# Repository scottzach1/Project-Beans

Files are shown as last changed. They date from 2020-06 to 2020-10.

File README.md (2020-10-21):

# Group 3 - Project beans

## Welcome to Project Beans.

Project Beans was a 2020 project by 6 VUW Engineering students to
deliver a model rocket for a client. An in-depth breakdown of the
projects scope, deliverables and current state can be obtained in-depth
within the documentation of this repository.

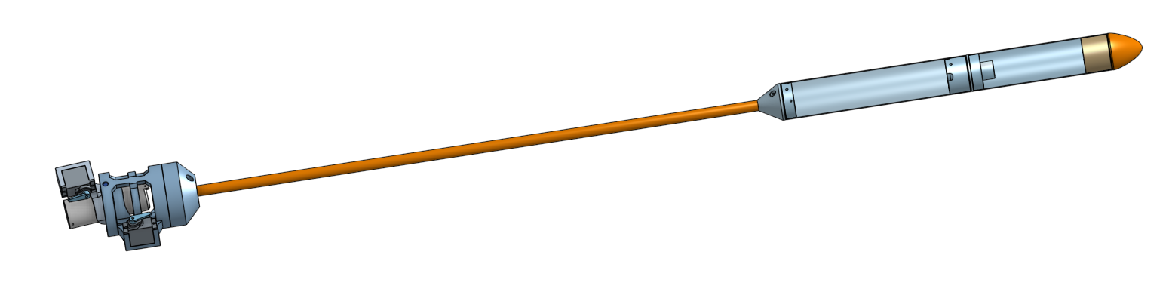
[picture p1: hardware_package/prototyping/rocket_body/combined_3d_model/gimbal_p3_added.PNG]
Rocket Design


> Figure 1: Rocket Design Render

## Meet The Team

### Software

| Zac Scott (https://github.com/scottzach1) | Ron Crisostomo (https://github.com/crisosron) | Finlay Sargisson (https://github.com/sarrgi) |
|:---|:---|:---|
| [Zac Scott](https://github.com/scottzach1) | [Ron Crisostomo](https://github.com/crisosron) | [Finlay Sargisson](https://github.com/sarrgi) |

### Hardware

| Niels Clayton (https://github.com/Niels-Clayton) | William Fowler (https://github.com/Will-Fowler) | Billy Rob (https://gitlab.ecs.vuw.ac.nz/robbbill) |
|:---|:---|:---|
| [Niels Clayton](https://github.com/Niels-Clayton) | [William Fowler](https://github.com/Will-Fowler) | [Billy Rob](https://gitlab.ecs.vuw.ac.nz/robbbill) |

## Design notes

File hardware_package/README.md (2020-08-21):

# Hardware Package

This directory is for all hardware related files, such as PCB designs,
CAD files etc...

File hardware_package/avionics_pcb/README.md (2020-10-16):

# Avionics PCB's

> Description of the different avionics PCB's and libraries

## KiCad

- All PCB's will be designed using the KiCad Cross Platform and Open Source Electronics Design Automation Suite. A selection of custom footprints and symbols used in the following projects can be found in the `kicad_lib/` directory.

- All PCB's within this directory will be subject to standard ERC and DRC rule checks, which will be performed and checked by the CI pipeline.

## PCB's

| File | Description |
|:---|:---|
| `avionics_base_station/`  | The avionics base station PCB will be used to connect the RFM98 LoRa radio to the [ESP8266 microcontroller](https://www.espressif.com/en/products/socs/esp8266), maintaining a small form-factor. This board is designed to be the final base station product. |
| `avionics_breakout_PCB/`  | The avionics breakout PCB will is the second prototype of the rocket hardware. This PCB will take all of the testing breakout boards that can be found [here](../bill_of_materials/bill_of_materials.md) in the BOM, and will integrate all of then onto a single compact board that is limited to a single side. This board will be used for extensive testing of the hardware in unison. |
| `Final_PCB/` | The avionics final PCB is the final iteration of the PCB. This board will take all of the individual components found on each of the breakouts, and will place them onto a single PCB. This board will also include power supplies for all components, including the ignition circuitry and servo motors.  |

## Libraries

| File | Description |
|:---|:---|
| `kicad_lib/` | This directory contains a selection of custom footprints and symbols that have been used in the PCB's. This library currently contains footprints for the following parts:

- Adafruit Feather STM32F4D5 Breakout
- ESP8266 Node MCU microcontroller breakout
- Adafruit MPL3115A2 Barometer Breakout
- Adafruit MPU 6050 Breakout
- RFM98 LoRa Radio

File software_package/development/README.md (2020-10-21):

## Development

The project structure  is covered in the `software_package` 
[README](../README.md), if you wish to understand more about this then 
go there. This README entails an overview of each of our libraries which 
can be found inside this package.

### Hardware

This library is specific to the exact hardware components which we have
used for this project. The key goal of this is to provide an API which
allows for abstraction away from the specifics parts for each type of
hardware component. For example, through this library the software
library is able to interact with the MPU-6050 by treating it as any IMU.
You're able to find the exact hardware library which is being abstracted
away from inside of `.pio/libdeps`.

Each component is represented with a header file (.h), as well as a
concrete implementation (.cpp). This separation of components allows for
maximum flexibility and reuse. If one specific component is upgraded or
replaced then only the relative header and implementation file should
need modifying.

### Current State

Towards the end of development for this project, there was a significant
update to platformio that changed how some of the libraries were
handled. This change, inherently broke the builds on a lot of the team
members devices. For some devices, this can be mitigated by installing
the `Servo` package to the project locally. Then manually moving it into
the `~/.platformio/lib/` directory (global libraries). There were
occasionally issues regarding the i2cdev libraries for the MPU6050 after
integration with the rest of the code base.

### Component Library Breakdown

| Component | Description |
|:---:|:---|
| Barometer | This is based off of the `Adafruit_MPL3115A2.h` library. The key functionality of this is reading air pressure and altitude data. |
| IMU | This was originally based off of the `Adafruit_MPU6050.h` library. To get more accurate readings this has since been switched to `I2Cdevlib-Core` and `I2Cdevlib-Core`. This allows us to be able to read quaternion values that are inherently less prone to errors and gimbal lock. In general, the main purpose of this is to perform the accelerometer and gyroscope readings. |
| Parachute | This component is still in development, but aims to simply handle the launching of the parachute ejection charges. |
| SD | This is based off of the `STM32SD.h` library. The primary functionality for this is performing file reading and writing on the SD card. |
| Servo | This makes use of the `Servo.h` library. The goal of this component here is adjusting and controlling the angle of the servo. |

### Software

This library aims to handle all the logic for our rocket, and works in
tandem with the hardware library to achieve this. As it is more
abstracted away than the hardware library it is designed to be robust
enough to be used with different hardware components. Small things, eg.
tuning a value to match a new part speed, may need updating when
replacing and upgrading components, but the core logic should be
relatively versatile.

| Component | Description |
|:---:|:---|
| Debug | This file is used for debugging messages related to our hardware. It can be used for writing and testing code, as well as pre-, post- and in-flight analysis. |
| States and State Machine | The state machine handles the current state of the rocket, and how to transition between them. States contains all potential states the rockets' system can be in. For a more in-depth explanation see section 4.1 of the [architecture](../../architecture_design/architecture-design.md) document, which covers the flow this software is modelled around. |
| Guidance System | This is essentially the main process of our rocket. It handles all the logic necessary to function, such as the pid, state machine, and all hardware communication. |
| Logging | This component handles sending data to both the SD card and LoRa radio. |

### Installed Packages
```bash
'Adafruit GFX Library'/
'Adafruit ILI9341'/
'Adafruit BusIO'/
'Adafruit MPL3115A2 Library'/
'Adafruit STMPE610'/
'Adafruit TouchScreen'/
'FatFs'/
'I2Cdevlib-Core'/
'I2Cdevlib-MPU6050'/
'STM32duino STM32SD'/
```

How to build PlatformIO based project
=====================================
Keep in mind that this entire directory _is_ a PlatformIO project. The steps below
outline how to build this project.

1. `Install PlatformIO Core <http://docs.platformio.org/page/core.html>`_
2. Download `development platform with examples <https://github.com/platformio/platform-native/archive/develop.zip>`_
3. Extract ZIP archive
4. Run these commands:

```bash
    # Change directory to example
    > cd platform-native/examples/hello-world

    # Build project
    > platformio run

    # Run program
    > .pioenvs/native/program

    # Clean build files
    > platformio run --target clean
```

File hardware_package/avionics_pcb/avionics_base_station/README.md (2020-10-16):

# Avionics Base Station PCB

This PCB is designed to interface the NodeMCU microcontroller with the RFM98 radio module. This board will act as the base station that will connect the ground control computer.

This PCB has been designed for a single layer, meaning that it is feasible to mill this PCB.

To assemble this unit, either directly solder the NodeMCU unit to the board, or solder on female headers with which to connect it. Then solder on the RFM98 castellated module and connect a solid core wire to the antenna.

## Schematic

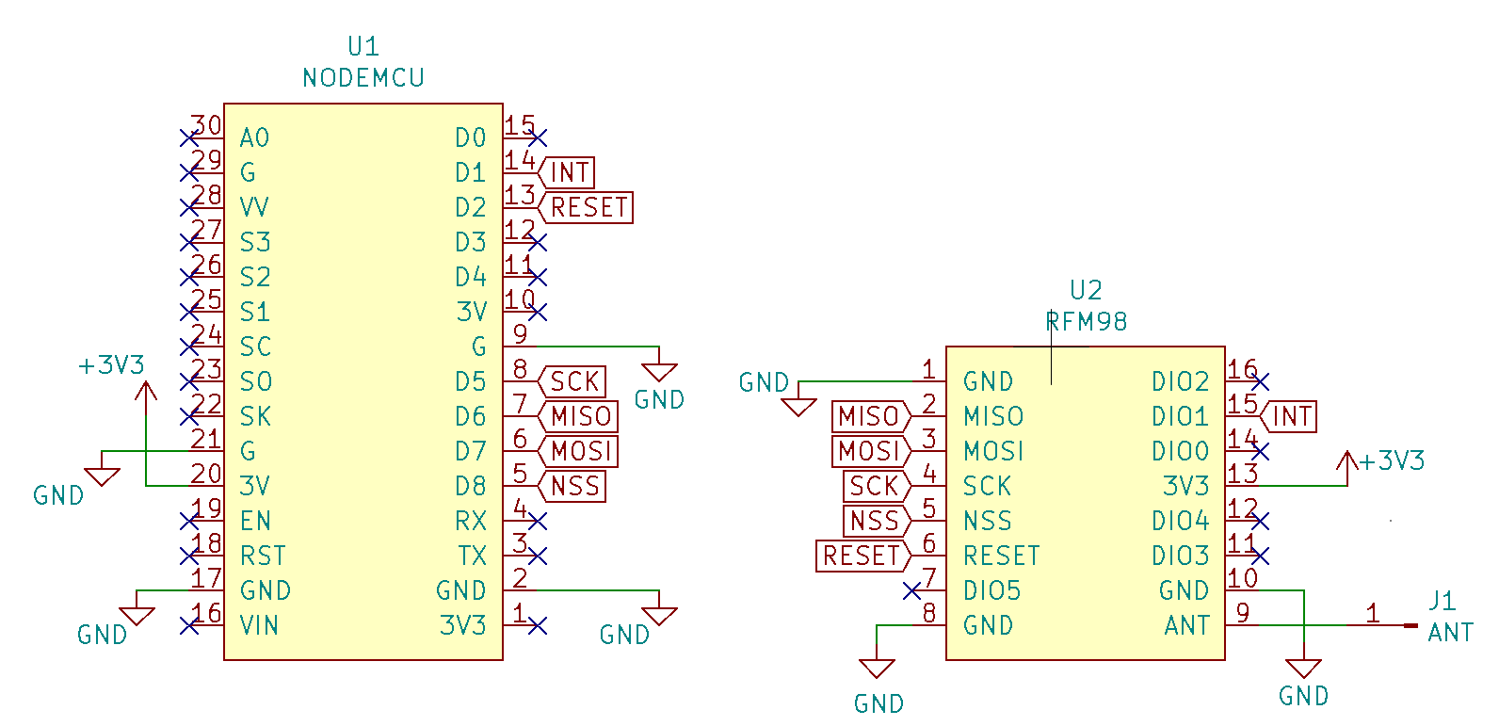
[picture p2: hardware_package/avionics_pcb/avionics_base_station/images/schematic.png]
schematic


## PCB Routing

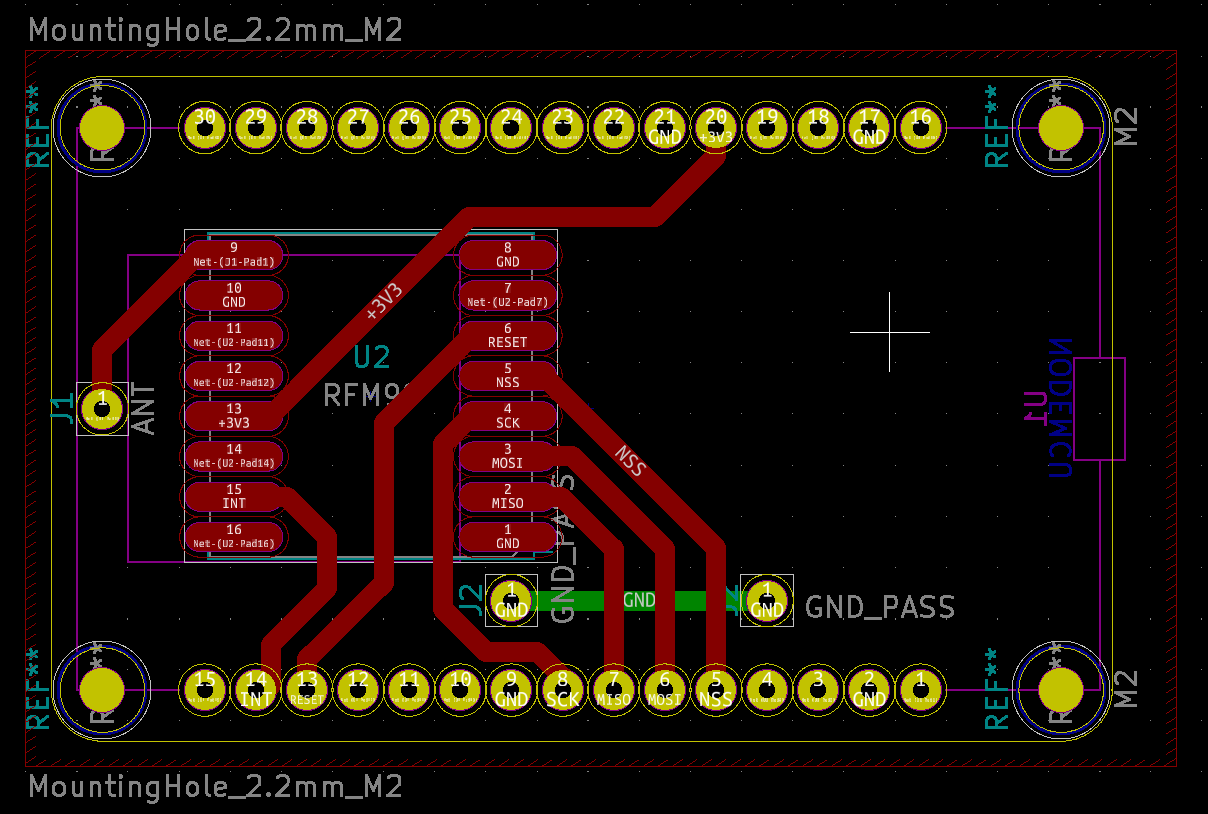
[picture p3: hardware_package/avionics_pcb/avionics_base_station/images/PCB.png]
PCB
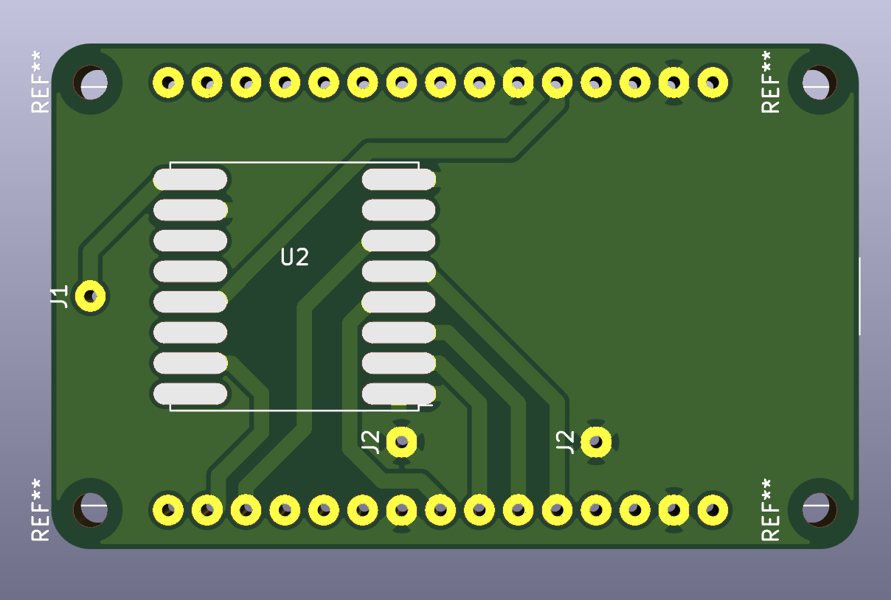
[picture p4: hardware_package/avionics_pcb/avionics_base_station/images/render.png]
render
 

## Assembled Unit

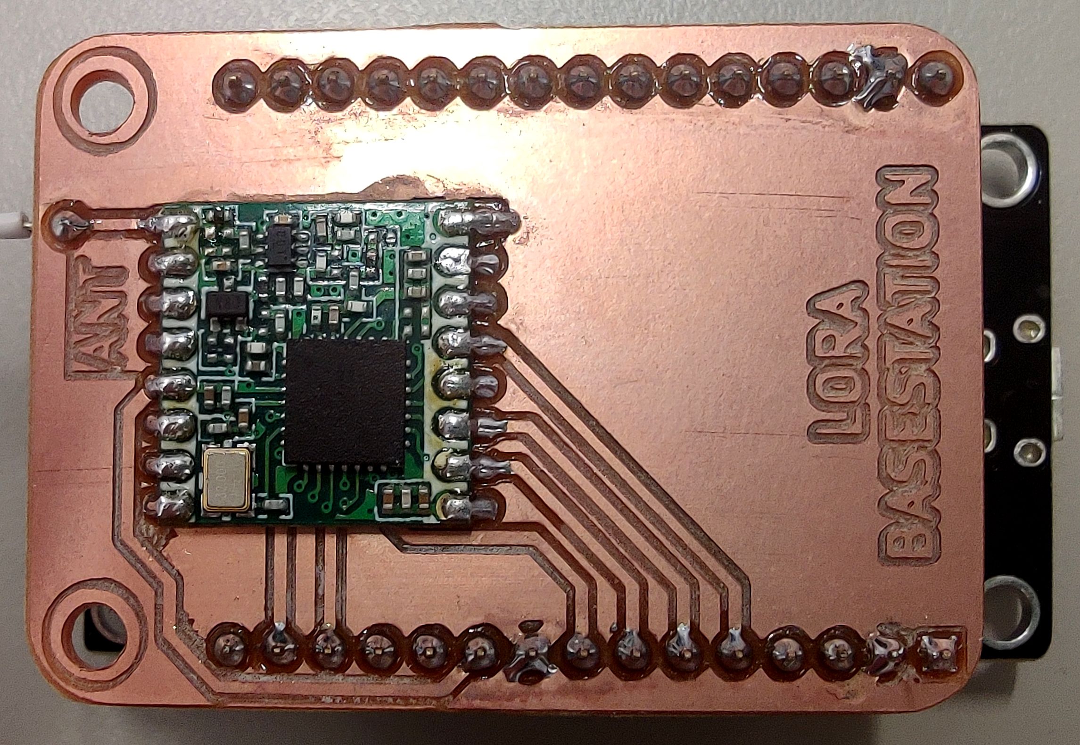
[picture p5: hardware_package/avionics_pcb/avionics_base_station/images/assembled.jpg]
assembled


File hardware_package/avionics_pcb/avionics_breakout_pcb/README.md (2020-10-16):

# Avionics Component Breakout PCB

This PCB is the second iteration of the avionics PCB, and is designed to interface the FeatherSTM with the MPU605 IMU, MPL3115A2 Barometer, and RFM98 LoRa module. This PCB is also design to breakout the UART serial connection needed for the GPS, as well as connections to the gimbal servos and 4 ignition lines.

This PCB is designed to be milled, and is therefor almost completely single sided. There will however need to be one mod wire connected if this PCB is milled on one side, which will connect the LoRa interrupt line to the interrupt pin.

To assemble this unit, either directly solder the components to the board, or solder on female headers with which to connect them. Then solder on the RFM98 castellated module and connect a solid core wire to the antenna.

## Schematic

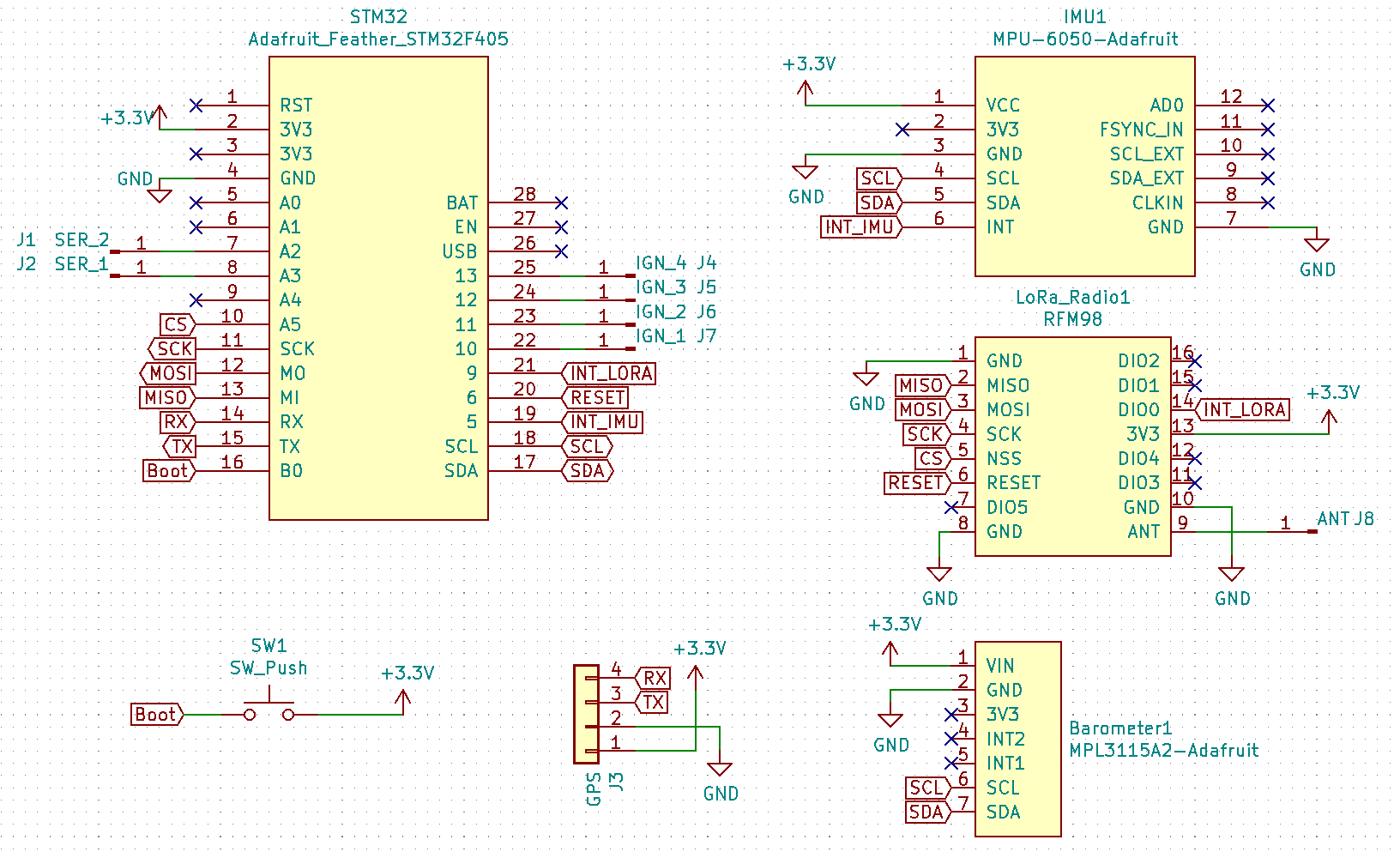
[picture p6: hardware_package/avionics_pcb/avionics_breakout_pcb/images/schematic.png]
schematic


## PCB Routing

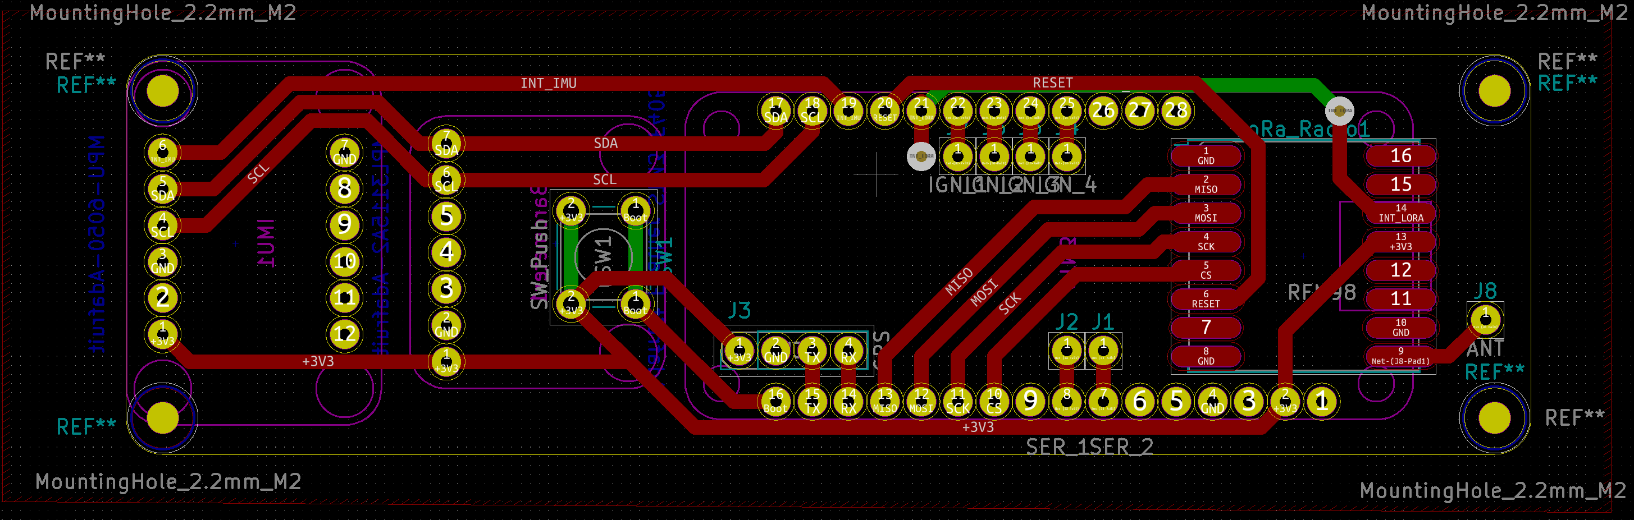
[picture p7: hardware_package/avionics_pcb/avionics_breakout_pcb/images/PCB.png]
PCB
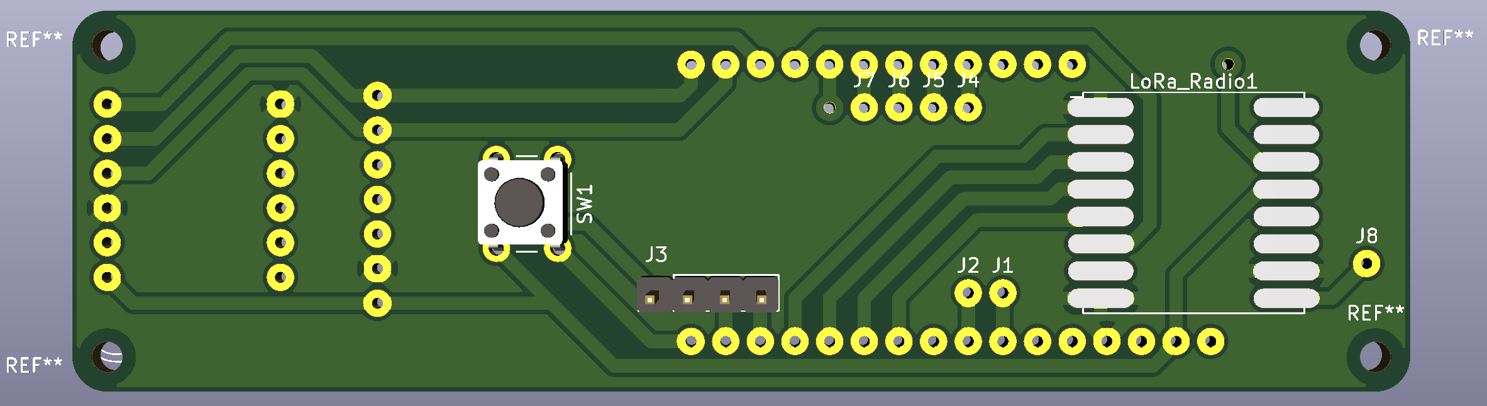
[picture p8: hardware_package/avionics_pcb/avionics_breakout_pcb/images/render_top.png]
render_top
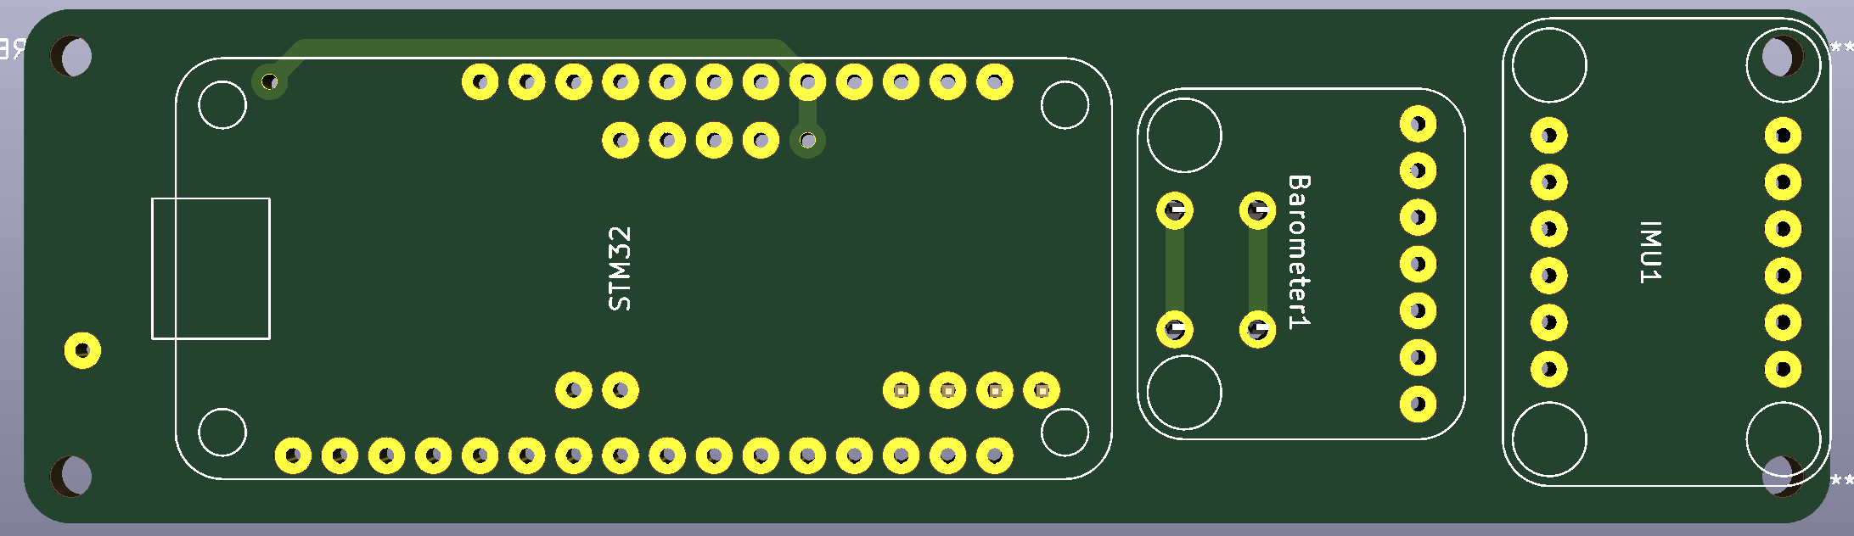
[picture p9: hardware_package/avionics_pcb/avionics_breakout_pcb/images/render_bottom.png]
render_bottom
  

## Assembled Unit

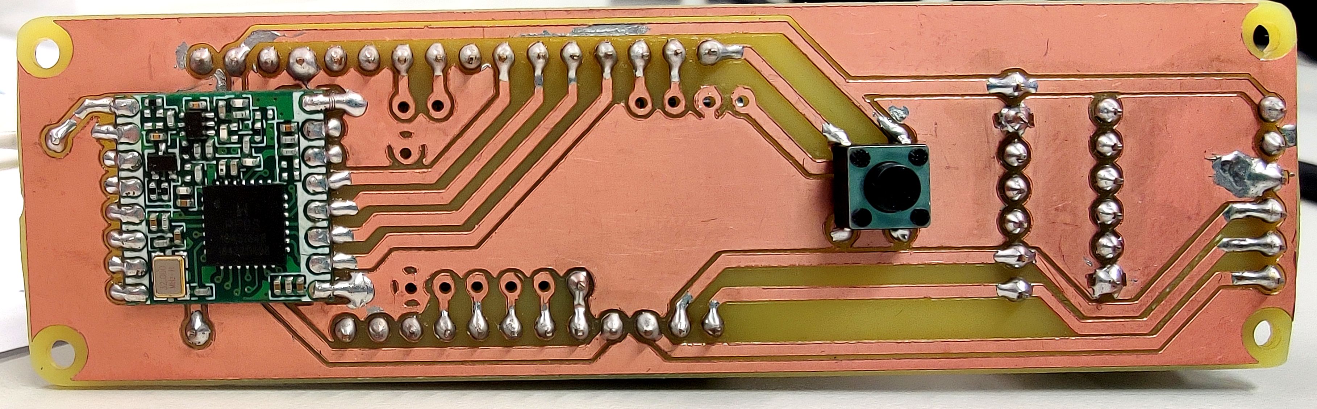
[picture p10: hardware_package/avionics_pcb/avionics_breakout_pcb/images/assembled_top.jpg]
assembled
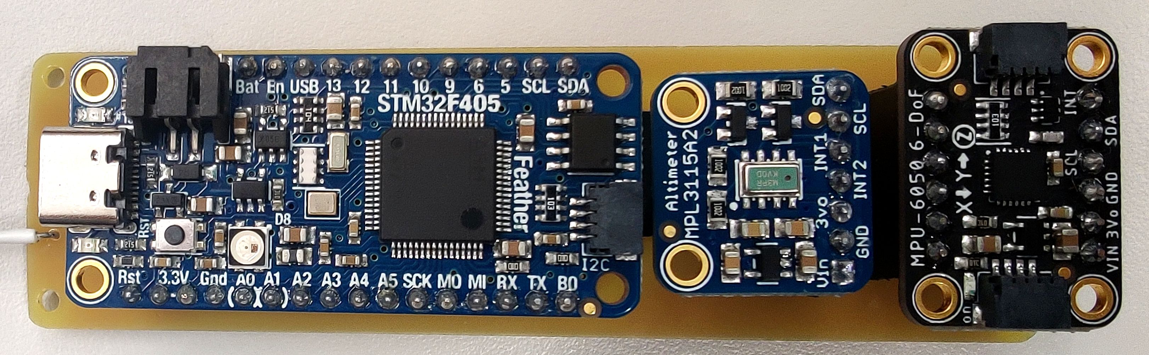
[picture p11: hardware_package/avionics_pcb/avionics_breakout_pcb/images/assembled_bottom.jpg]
assembled


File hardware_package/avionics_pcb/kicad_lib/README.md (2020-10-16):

# Avionics KiCad component library

This library contains all custom footprints and symbols that have been designed for use on the avionics PCB.

## Symbols

### Feather STM32 Breakout Symbol

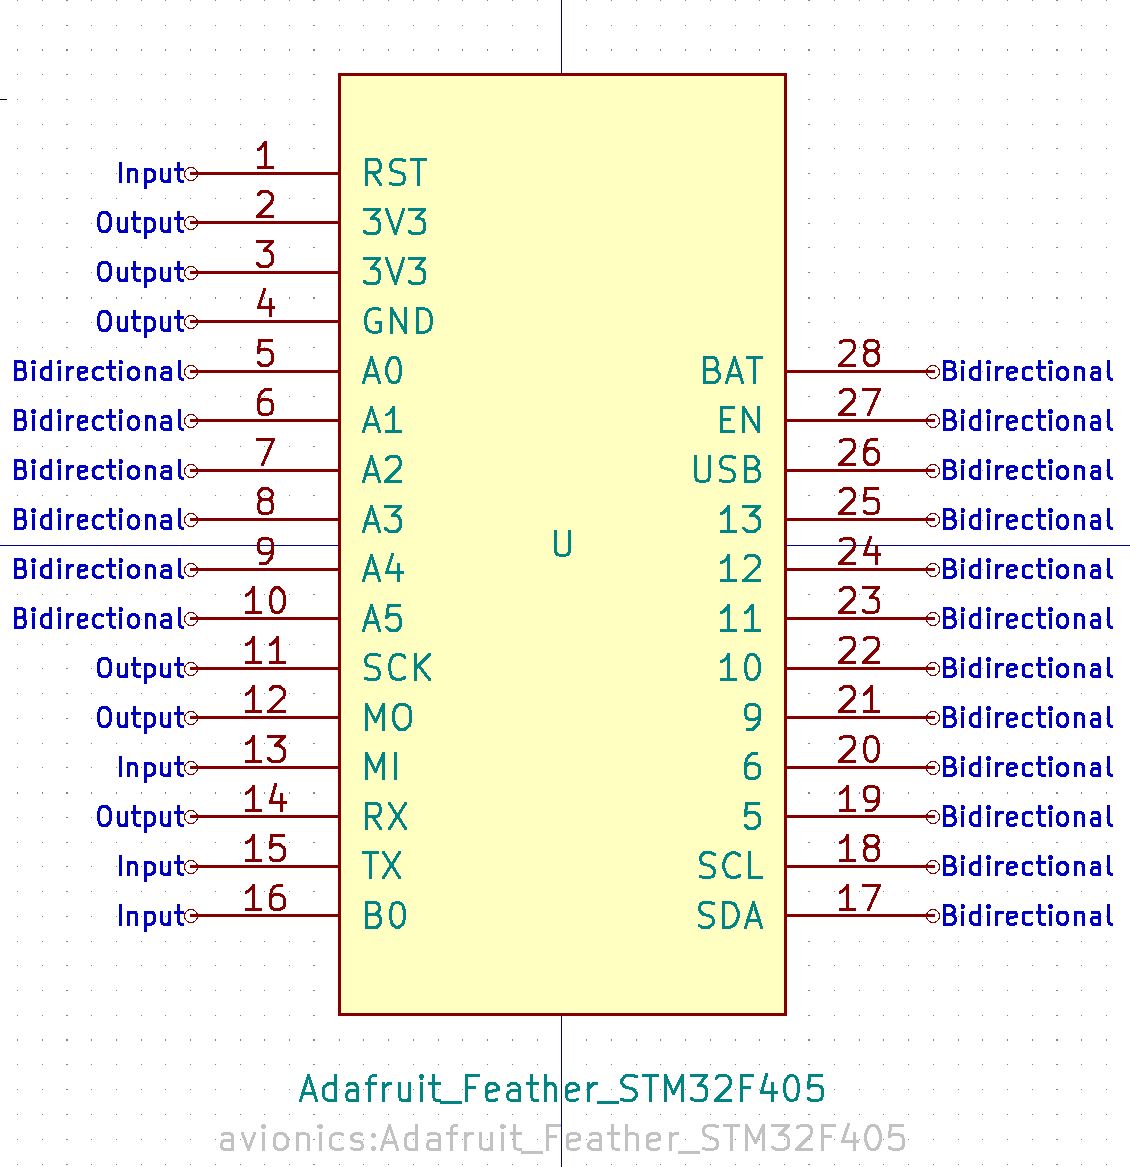
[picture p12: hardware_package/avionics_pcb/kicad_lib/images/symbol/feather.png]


### NodeMCU Breakout Symbol

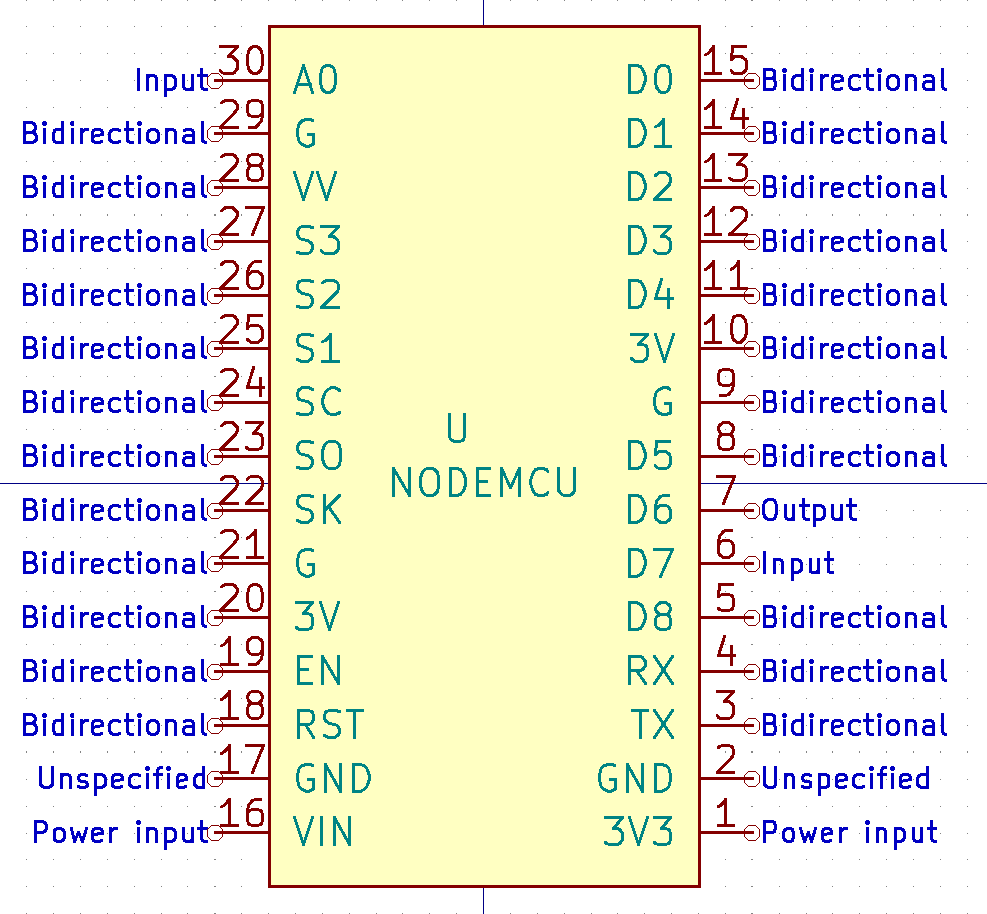
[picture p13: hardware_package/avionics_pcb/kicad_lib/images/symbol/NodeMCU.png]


### MPU6050 IMU Breakout Symbol

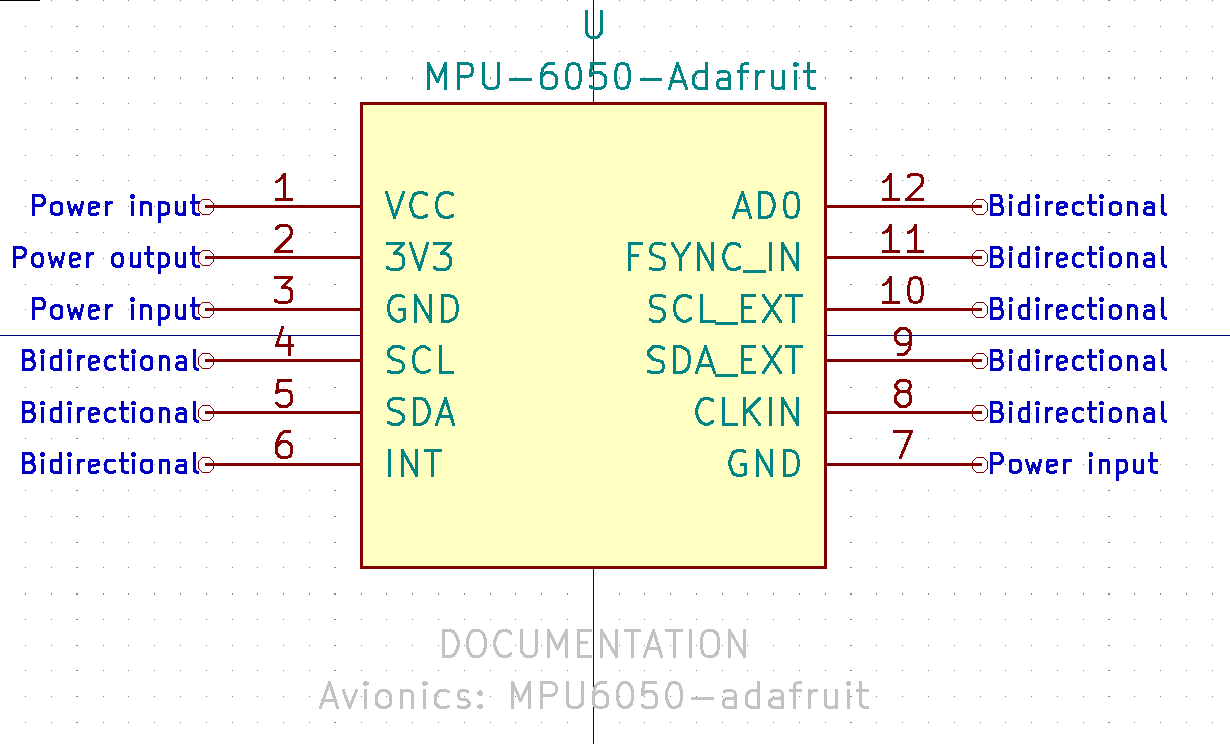
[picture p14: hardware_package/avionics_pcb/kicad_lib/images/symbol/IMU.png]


### MPL3115A2 Barometer Breakout Symbol

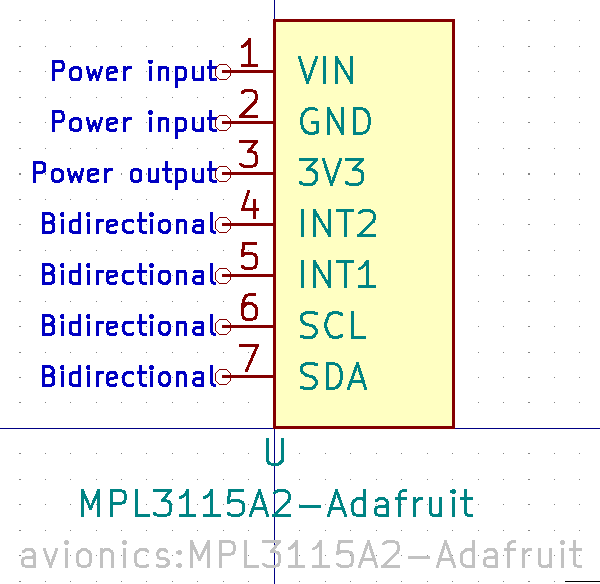
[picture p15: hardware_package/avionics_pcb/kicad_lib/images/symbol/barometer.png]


### RFM98 LoRa Radio Breakout Symbol

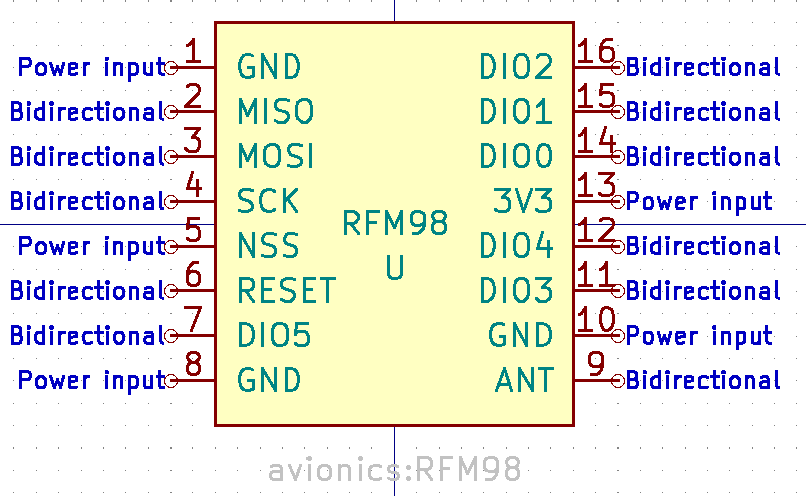
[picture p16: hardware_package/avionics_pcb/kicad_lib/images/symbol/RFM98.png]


## Footprints

### Feather STM32 Breakout Footprint

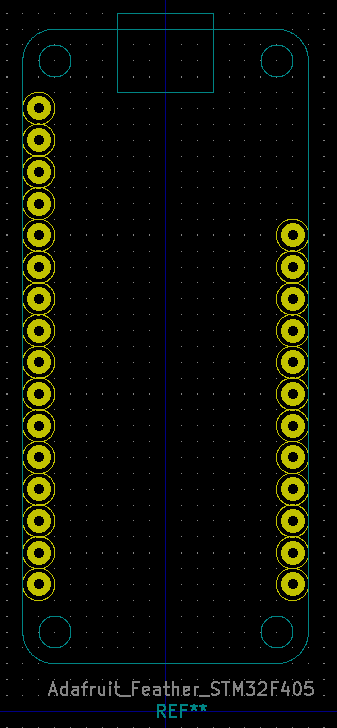
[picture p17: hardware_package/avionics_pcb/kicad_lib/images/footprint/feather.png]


### NodeMCU Breakout Footprint

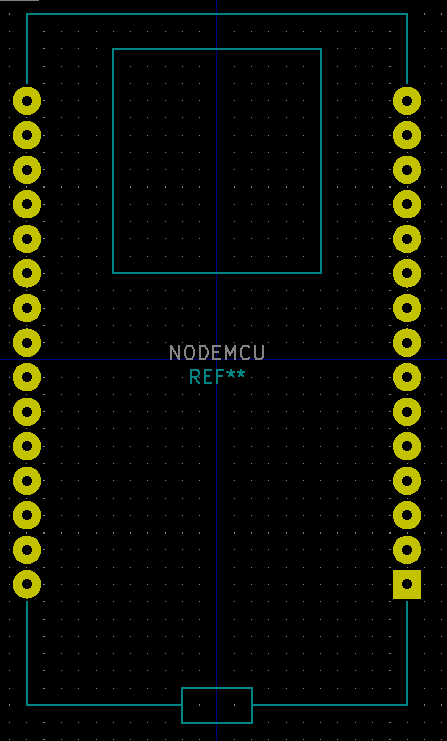
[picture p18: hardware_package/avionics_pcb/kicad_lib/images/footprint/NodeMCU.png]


### MPU6050 IMU Breakout Footprint

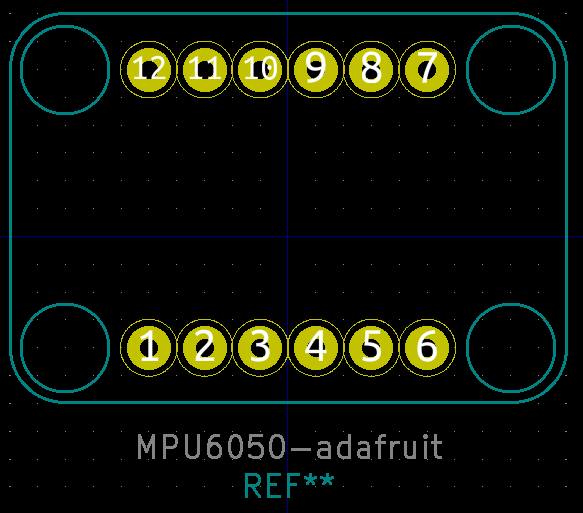
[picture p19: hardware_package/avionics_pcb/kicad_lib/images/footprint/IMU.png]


### MPL3115A2 Barometer Breakout Footprint

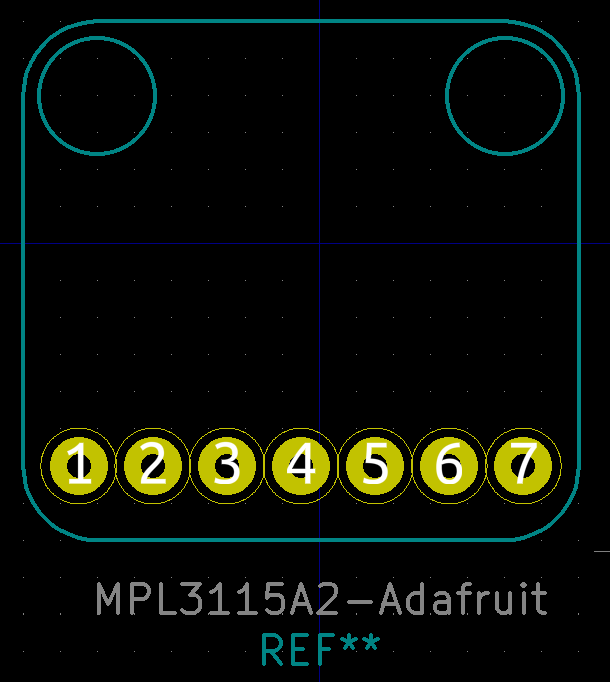
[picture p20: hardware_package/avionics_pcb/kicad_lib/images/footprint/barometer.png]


### RFM98 LoRa Radio Breakout Footprint

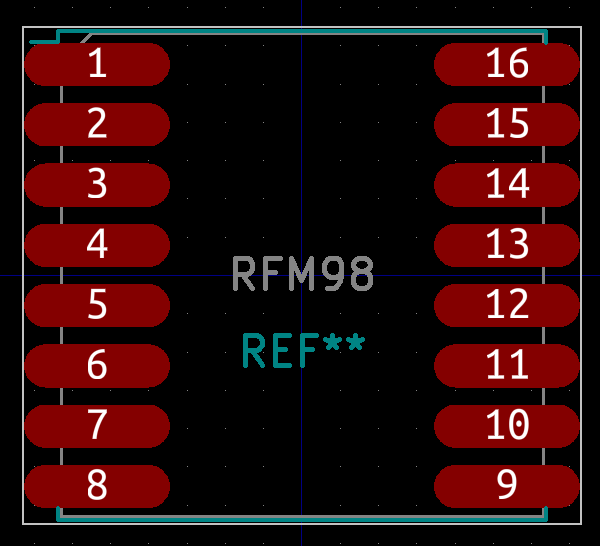
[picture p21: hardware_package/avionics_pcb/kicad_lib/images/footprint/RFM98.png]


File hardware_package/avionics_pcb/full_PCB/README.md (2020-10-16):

## Full PCB - Prototype 1 - Documentation

This PCB is designed to accomodate the STM32F405 processor, the accompanying sensors and peripherals, power circuitry and supporting passive and active electronic components required by the avionics package.

### Schematic
For the schematic we wanted to integrate as many components into the avionics package board as possible to reduce the size and cost associated with manufacutring. In this case the only sensors that are not integrated into the board are the MPU-6050, the GPS and the LoRa radio tranceiver which are on breakout boards connected by headers.

#### Power circuitry
The avionics package is designed to be powered off of a 2-cell LiPo battery supplying a nominal voltage of 7.4V. This is connected to the avionics board via a 3 pin JST connector. Included in series with the +7.4V pin is a fet and polyfuse to protect against reverse polarity and over current. The 7.4V is then passed to two regulator, a 3.3V linear regulator capable of supply up to 1A for the microprocessor and periphals and a 6V switching regulator capable of supplying up to 2A to both of the servos. So there is a +3.3V and a +6V rail. The ground is referenced to the negative terminal of the battery.

Regarding the 3.3V regulator, a fet and diode are included at the input so that when the battery is connected the 5V supplied by the voltage bus of the USB-C port is cut off by the fet. If the battery is not connected then the device can be powered off of the USB-C port. For verification and debug purporses, LEDs and test points were included at the output of both regulators and an additional test point included for ground. Lastly decoupling capacitors were included between the power rails and power inputs of each of the ICs to isolate any potential noise sources from interfering with the rest of the system.

#### STM32F405 and Adafruit feather design
The STM32F405 was chosen as our design is based on the Adafruit STM32F405 Feather Express development board [available here](https://learn.adafruit.com/adafruit-stm32f405-feather-express/downloads). From this development board we kept the microSD port, the USB-C connector, flash memory, and a redesigned 3.3V regulator. Components and features that we did not integrated from the Adafruit Feather included the USB battery charger and NeoPixel programmable LED. The battery charger was not included as this functionality would make the avionics package bulkier and it is not practical to charge a 2-cell LiPo using USB.

Both of the external oscillator crystals included in the Adafruit feather were not included in the design as the STM32F405 already contains a high speed internal RC oscillator which runs at 16MHz.

#### Sensors and peripherals
For the sensors and periphals, included in the schematic are the IMU, Lora radio tranceiver, barometer and GPS. All of these aside from the barometer are integrated into the PCB. The IMU, radio and gps have pads to connect the breakoutboards for these components via headers. The GPS, barometer and IMU all communicate via I2C protocol while the flash memory and radio module communicate via SPI protocol.

All the sensors and breakout boards are based off of Adafruit designs listed below:
[GPS](https://learn.adafruit.com/adafruit-mini-gps-pa1010d-module)
[Radio Tranceiver](https://learn.adafruit.com/adafruit-rfm69hcw-and-rfm96-rfm95-rfm98-lora-packet-padio-breakouts/downloads)
[IMU](https://learn.adafruit.com/mpu6050-6-dof-accelerometer-and-gyro?view=all)
[Barometer](https://learn.adafruit.com/using-mpl3115a2-with-circuitpython)

### PCB design
The PCB design uses 4 layers, the top and bottom are for signals, the 2nd layer is a ground plane and the 3rd layer is a +3.3V plane. The PCB can be sectioned into the power supply, breakout board pads, microprocessor, microSD card port, flash memory and barometer, all including their respective supporting components. Most of the anlogue circuity was segrated from the digital components to minimize EMI.

In terms of footprints, aside form the breakoutboard pads, pads for the futaba JR connectors, the poly fuse and flash memory, all the other footprints are surface mounted. This is to ensure the package remains small and compact.

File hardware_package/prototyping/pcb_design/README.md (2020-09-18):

## Rocket PCB Design

Documentation on SD card reader/writer pinout available
[here](https://pinouts.ru/visual/gen/sdcard.jpg):

Need to determine whether it will operate in SD or SPI mode.

#### Notes:

- The battery charger is only capable of charging one cell in the battery,
a potential work around for this could be to include two battery charger units
and have them operating in parallel. Alternatively, could buy an external
battery charger or charge individual cells sequentially.

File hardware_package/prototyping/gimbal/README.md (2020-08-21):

# Gimbal Prototyping Document

This document will contain progress of the gimbal and any important
decisions made at each stage. Measurements and requirement will be
included also.

| C class | D class | E class | F class | |
|:---|:---|:---|:---|:---|
| **Diameter (min)** | 18mm | 24mm | 24mm | 29mm  |
| **Length (min)** | 70mm | 70mm | 95mm | 114mm |

## Prototype 1

Log:
- Prototype 1 Gimbal components created in Onshape (sprint 4)
- Assembly of components and servos finished in Onshape (sprint 5)
- ToDo: Print Prototype 1 in sprint 5

### Considerations for P2 based on P1

- There are a few sections on corners that are too thin and may break.
  These must be filled out.
- There are several considerations regarding bolt mounts that must be
  changed.
  - Must be reinforced else bolts will crack the plastic.
  - Diameter of holes should be 0.2mm less than the bolts, this will
    allow the bolt to thread the plastic.
  - Nuts are not entirely necessary for servo mounts. Can just make
    deeper holes.
- Servo Measurements were incorrect in P1.
- P1 has 20 degrees of freedom in one axis and 10 in the other. This
  seems sufficient and should be retained.
- Generally thicker to ensure strength.
- Should minimize overhangs for better printing.
- P2 should have mounts for the rocket, distance between center of mass
  and gimbal rotation axes must be considered (cannot be too small else
  insufficient torque on the rocket for change of angle).

## Prototype 2

Specs:

- M3 bolt size (8-9mm long partially threaded) (Servo screws are M2.5
  (x4))
- If length is not 8-9mm the design will need to be modified to account
  for this.
- another option for bolts/screws is using nuts but embedding them in
  the design (will required modification).
- Motor diameter 24mm

**Log: Create and assemble prototype 2 (for 24mm engine)**:

- Made Gimbal Tube
- Made inner and outer rings where axes of rotation are mounted.
- Added upper and lower servo mounts to rings
  - Mounts are made to be the same offset from their respective axis of
    rotation. This is to ensure same angle change, show make control
    system easier to tweak.
- Added structural support to servo mounts.
- Screw holes added to mounts.
- Created Assembly.
- added anchor for wire that attaches to servo lever.
- May require changes based on selected bolts.

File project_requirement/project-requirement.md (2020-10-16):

# ENGR 301 Project Beans Project Proposal and Requirements Document

[[_TOC_]]

## Authors

Billy Robb, Niels Clayton, Finlay Sargisson, William Fowler, Ron
Crisostomo, Zac Scott.

---

## 1. Introduction

Rockets ranging from NASAs Saturn V to an amateur's first model rocket
require stability in order to perform as intended. The method in which
stable flight is achieved varies to a large degree, but can be divided
into two basic categories. The most common being passively stabilized
rockets. These maintain a stable flight due to passive aerodynamic
features, an example being fins that give the rocket a stabilizing
rotation (similar to the effect of rifling on a bullet). The simplicity
of a passive system is appealing but any error introduced to the system
can cause an unwanted flight trajectory. Some examples of such errors
include, unexpected wind or differences in fin sizes which are not
accounted for in the design. The second category is an active control
system. Onboard electronics can be used to achieve active course
correction. Error in the rocket's trajectory can then be mitigated in a
way that passive systems cannot. The drawbacks of this are the
complexity and large overhead introduced when constructing the rocket.

Our customer has plans to eventually launch a rocket from a weather
balloon at approximately 70,000ft. This application requires the use of
an active control system. Existing off-the-shelf avionics packages for
amateur rocketry enthusiasts are available, however, do not meet the
full requirements of our customer. This is due to limited functionality
and the need for software to be open source to allow for further
development of the package at a later date. In conjunction with
implementing an active control system this project also aims to improve
on a previous design provided by a team in 2018. This project will also
be running in parallel with two additional projects (mission control and
simulation) to provide the customer with a comprehensive solution.

### Client

Our client for this project is Andre Geldenhuis. Andre is a rocket
enthusiast who is part of the NZ Rocketry Association. As of writing
this this their contact email is "andre.geldenhuis@vuw.ac.nz", and
throughout the project the team can also contact Andre via a live text
chat (Mattermost Customer channel).

### 1.1 Purpose

The purpose of this system is to create a rocket which can be controlled
in flight while remaining open source and accessible, so that it can be
further developed by the amateur rocketry community, and contribute to
the existing body of knowledge.

### 1.2 Scope

The objective is to deliver an avionics system that will allow stable
controlled flight while simultaneously logging and broadcasting data.
This system should improve on the existing avionics package created by a
team in 2018 for Andre. There is no requirement on height or flight
time, only to demonstrate controlled flight. The flight data must be
logged to an onboard SD card, and the broadcast data must be accessed in
real-time by an onsite personal computer (base station). The rocket must
also, upon request, be capable of broadcasting its current location via
GPS. The rocket is expected to support C or D class solid fuel rocket
motors. The key improvements as compared with the 2018 avionics package
are, a reduction in onboard PCB size and reliability in the field. To be
considered more reliable the avionics package should initialize and
launch on the first attempt. The package must also not have loose wires,
exposed electronics and implement robust code to support this.

### 1.3 Product overview

#### 1.3.1 Product perspective

There is no specific larger project that this system will be integrated
into, rather it is intended to contribute to our customer's long term
ambitions and the body of knowledge in the amateur rocketry community
alike. Our client is aiming to one day launch rockets from a weather
balloon. This will require a system that can launch and achieve stable
flight from a platform with active control. Due to this the project's
main focus is on designing a robust active control system that can be
adapted later on to help the client reach their goal.

This project is open source, allowing the final product to be tweaked
and repurposed by the community. This adds longevity to the project
after it is officially ended. This can benefit the customers as this may
result in further development by the community.

A similar open source project was produced in 2018 for our customer.
Therefore, this project, where needed, will make use of existing
resources to ensure an improved solution is provided to the customer.

#### 1.3.2 Product functions

The requirements specified for the client's minimum viable product
include:

##### Base functionality Requirements

- A rocket that achieves stable flight with an active control system
  without the use of a launch rail.
- Records data from all sensors at a rate where the flight path could be
  reasonably reconstructed post flight.
- Broadcasts radio telemetry and battery level during the launch, burn
  and post-burn phase of flight.
- Recovered post flight without sustaining significant damage to the
  electronics.

##### Required functionality Improvement

- Software can be reliably initialized in the field.
- Software is held to a high level of quality and robustness.
- Must have protected electronics, wires and PCBs cannot be exposed.

#### 1.3.3 User characteristics

One of the key requests from our client is that the avionic package will
be open source, which allows use and potential continuation of this
product from anyone in the wider amateur rocketry community. Future
users could include but it not limited to students, researchers,
programmers and rocketry hobbyists.

Since there is a wide variation in potential users, it is recommended to
have experience in certain technical areas prior to developing parts of
this project. These include:

- When installing the electronic components.
- Interfacing between the software and hardware.
- Complying with Civil Aviation Authority Regulations.
- Configuring telemetry functionality.
- Operating aircraft applications

Users should have an understanding of how this package will be applied
to their own specific projects. It's also important that the users are
able to fully comply with all of the health and safety regulations
required by their local authority on civil aviation if a rocket is
to be launched.

#### 1.3.4 Limitations

**Sensor Data and broadcasting limitations**:

One of the main requirements is to store sensor data. This must be done
at a fast enough rate. Not all of the sensors have the same polling
speed so the complete state of the rocket (as seen through the sensors),
can only be updated at the rate of the slowest sensor.

Terrain, distance and weather conditions will affect the strength and
reliability of the broadcast data to the base-station. This will limit
the range and conditions in which the rocket can operate in. The rocket
should only be operated granted line of sight to the base station to
ensure a reliable connection.

GPS data is also likely to become inaccessible during flight. This means
that there should be no in flight dependencies placed on this data.

**Conditions**:

The rocket is not designed to be waterproof, neither is the control
system designed to handle interaction with rain and high wind speed.
Therefore, for protection of the onboard electronics, the rocket should
be launched only on clear days with a wind speed less than 10 knots.

**Launch sites**:

Due to the dangerous nature of a rocket, locations where the rocket can
be tested is limited. Open spaces with high visibility and with no
people within a safe distance are the required constraints.

---

## 2. References

\[1] “Rocket Safety,” NZ Rocketry Association. [Online]. Available: https://www.nzrocketry.org.nz/rocketry/rocket-safety. [Accessed: 30-Apr-2020].

\[2]
Part 101 Gyrogliders and Parasails, Unmanned Aircraft (including Balloons), Kites, and Rockets Operating Rules. [Online]. Available: http://www.aviation.govt.nz/rules/rule-part/show/101/4. [Accessed: 13-May-2020].

\[3]
“Vectored Thrust,” NASA. [Online]. Available: http://www.grc.nasa.gov/WWW/K-12/airplane/vecthrst.html. [Accessed: 13-May-2020].

\[4] “Licenses & Standards,” Licenses &amp; Standards | Open Source Initiative. [Online]. Available: https://opensource.org/licenses. [Accessed: 16-May-2020].

\[5]
“Radiocommunications Regulations 2001,” Radiocommunications Regulations 2001 (SR 2001/240) (as at 01 October 2017) Contents – New Zealand Legislation. [Online]. Available: http://www.legislation.govt.nz/regulation/public/2001/0240/latest/DLM71513.html. [Accessed: 02-May-2020].

\[6]
“Radiocommunications Regulations (General User Radio Licence for Short Range Devices) Notice 2019 - 2019-go1588 - New Zealand Gazette,” New Zealand Official Crest. [Online]. Available: https://gazette.govt.nz/notice/id/2019-go1588. [Accessed: 02-May-2020].

---

## 3. Specific requirements

### 3.1 External interfaces

#### Radio Antenna

The radio antenna will facilitate the transfer of data and commands
between the avionics package and the base station. This radio antenna
must allow for the live broadcast of the package's geographical location
data which will be provided by the GPS unit post flight. This will allow
for easier retrieval of the unit by the customer. While in flight, the
radio antenna will also facilitate the periodic sending of other sensor
data to the base station for use in live monitoring of performance. The
data to be sent will include the following but is not limited to:

- Current gimbal position/angle
- Directional acceleration data
- Battery voltage

This radio antenna will also allow for commands to be sent from the base
station to be received and processed by the avionics package. These
commands will be able to query a range of settings and readings
pertaining to the status of the avionics package as well as alter them.

#### External: SD Card

The avionics package will be required to facilitate the logging of
launch and flight data to an onboard SD card. The SD card will store
data provided by the inertial measurement unit, as well as the
geographical location data from the GPS unit. Following the retrieval of
the SD card, the data will then be compiled into a CSV file and saved to
the external drive. There the data can be used to analyze the
performance of the system during launch and flight.

Due to this functionality the SD card must be capable of writing data at
the same rate (or faster) than the rate it is polled from the sensors.
At the same time this process must not impact the performance of the
active control system.

#### External: Inertial Measurement Unit (IMU / Sensors)

In order to identify the relative position, momentum and orientation of
the rocket throughout flight, the avionics package needs to track its
linear and angular acceleration.

This is performed by the Inertial Measurement Unit (IMU) of the avionics
package. The IMU will be poll for for 9-axis gyroscopic data, as well
as linear acceleration data, which will be used to track the position
of the rocket relative to the launch site in real time. This is required
by the active control system and is also written to the SD card for
analysis and troubleshooting.

#### External: Guidance System

The avionics package will be required to facilitate controlled flight
with self correction. To achieve this, the avionics package will contain
a guidance system consisting of a tuned PID (proportional, differential
and integral) controller. This unit will take the IMU data as well as
the current position of the gimbal as inputs. It will then output
positional information which will be used to alter the current position
of the gimbal, in turn altering the position of the rocket via vector
thrust \[3]. The guidance system will be required to process this data
at the same rate it is polled from the IMU, allowing for real time
corrections. This guidance system will also log its outputs to the SD
card for analyzing the performance of the unit, and for tuning the PID
controller.

#### External: Gimbal

The avionics package will require a gimbal unit to interface with the
gimbal hardware of the rocket. This unit will be required to apply
positional changes to the gimbal, as well as keep track of the current
position of the gimbal, accounting for any drift in the positions of the
servos due to forces applied by the motor charge.

#### External: GPS

The avionics package will be required to facilitate the retrieval of GPS
coordinates. This GPS data must be accurate to within a 5 meter radius,
and will be passed to the radio antenna unit for broadcast to the base
station. This will be used to help locate the rocket after a successful
launch. The GPS unit will also log all of its outputs the SD card.

### 3.2 Functions

#### 3.2.1 Use Cases

There are not that many unique uses for this project, as this is
designed with the sole goal of creating a rocket which operates
autonomously after launch. As parts of this project contain dangerous
goods, it's not advised to use this package for different purposes
without careful consideration and alterations. That being said there are
still various interactions between users and the rocket.

**_Use Cases:_**

1. **Launch the Rocket:** This is a primary use case and therefore most
   important use case for this project.
2. **Transportation of Rocket:** It is important that the rocket is
   handled safely, and for this reason, it will be handled by a
   professional. The specifics of this are outlined further in the
   safety plan.
3. **Assembly of rocket:** The rocket is designed with different
   packages and components which must be assembled before launch. This
   is a process which should take less than 15 minutes, and is well
   documented in the supplementary assembly instructions.
4. **Disassembly of rocket:** This is important as the rocket needs the ability
   to add or remove components for a range of reasons, i.e. faulty or
   outdated components. It also allows future users to
   extend the product. This is also covered in the supporting assembly
   document.
5. **Reading of flight data:** It is important to record all flight
   data, as this provides the users insight as to why the system behaved
   as was observed. This data will be sent to the base station during
   flight, and is visible to the team positioned at the base station.
6. **Analysis of flight data:** In addition to reading the data, it is
   also important to formally record the data. This gives users the
   opportunity to perform further analysis, and to apply improvements
   for future launches.

#### 3.2.2 Requirements

This subsection is broken down into three subsections, and aims to
identify all of the requirements necessary for the product to perform
the use cases outline in the previous section. The functions specified
by the customer's Minimum Viable Product are of primary concern to best
ensure the project is considered successful. Following the minimum
viable product, additional functions specific to hardware and software
are listed which

**_Requirements / functions of the Minimum Viable Product_**:

1. **The Rocket is safe to transport:** As the motor is classified as a
   Class 1 dangerous goods (New Zealand Land Transport Rule: Dangerous
   Goods 2005) considerations regarding safety features and transport
   procedure are necessary. Included in the safety plan (section 2.2) is
   information detailing the necessary precautions and procedure.
2. **The rocket is re-usable:** The rocket is intended to support
   multiple launches. This ensures that the rocket is designed to a high
   standard and offers greater value to the customer. For these reasons
   the rocket is expected not sustain significant damage within the
   first ten launches.

3. **The group is able to conduct post flight analysis:** This means
   that all necessary flight data is recorded and sent to the base
   station during flight. This ensures that upon both successful and
   unsuccessful launches the team is able to further analyze the flight
   in detail.
4. **The rocket is tunable/tweakable for optimization:** This means that
   there are no unnecessary dependencies between packages. This should
   reduce "god objects" and help to make all packages as interchangeable
   as possible to provide the user with more options
   when attempting to optimize the system. It also means that once built,
   the rocket is able to be disassembled with relative ease.
5. **Once flashed the rocket can be assembled and ready to launch within
   15 minutes:** Essentially from starting the assembly process of the
   rocket it should be ready for launch within 15 minutes. This allows
   the user to perform multiple launches within any given excursion and
   capitalize on ideal environmental conditions. It also means more time
   can be allocated to minor tweaks at the launch site.
6. **The rocket consists of a single kit:** This means the rocket can be
   easily transported and decreases the risk of losing launch critical
   components.

**_Hardware Requirements_**

1. **Physically withstand high acceleration:** Due to the nature of model
   rockets, all components of the rocket must
   be able to withstand significant acceleration. It is crucial that no
   component becomes loose or dislodged during launch as this poses a
   safety risk and may also result in further damage to the package. To
   be conservative, the rocket must be rated for up to 20 meters per
   second per second of acceleration. To ensure the rocket meets this
   requirement, measures such as secure mounting and bracings must be
   implemented on the rocket.
2. **Safe and controlled landing:** Due to the potential altitudes of model
   rockets using class D and E motors, an uncontrolled landing can cause
   significant damage to both the rocket itself, as well as any people or
   objects in the surrounding environment. To ensure the rocket is safe,
   it is essential that the rocket performs a safe and controlled
   landing, without drifting too far from the initial launch position.
3. **The rocket fits within a 29mm airframe enclosure:** This hardware
   requirement is an extension of the usability requirement where the
   rocket must be contained within a single kit. The dimensions of the
   rocket would affect how its internal components are structured. A
   smaller rocket promotes efficient use of space and more affordable
   components.
4. **Rocket components must be easily accessible to the public:**
   As this rocket is to be open source. It is a requirement that all
   components can be reasonably obtained or produced by a member of the
   public. This extends the lifetime of the rocket and reduces the risk
   posed by unforeseen component failure. This also includes any parts
   used to produce or assemble the PCB / components of the rocket. 3d
   printed parts, will also contribute to the assembly to help achieve
   this.

**_Software Requirements_**

1. **Control system adaptation to varying wind velocities:** The Rocket's
   software must be capable of handling wind speeds up to and within the
   maximum wind threshold specified inside the safety document. This
   requires the control system to offset any biases and deviations
   introduced by the weather conditions.

2. **Logging:** The rocket must log all flight data. This will include
   the logging of all internal sensor data, as well as commands issued to
   the IMU. The components in particular whose readings should be logged
   include the IMU, Radio and GPS. The readings must be logged to a file
   within the SD card for post launch analysis as well as critical data
   broadcast over LoRa.

3. **Mid-flight error correction:** The rocket's software must attempt to
   perform in air error analysis. This critical component of the rocket
   is fundamental to the safety of the rocket and any people or objects
   in the surrounding area. It is critical the rocket can respond
   correctly to erroneous data. Erroneous data could be observed via any
   readings from components whose output is part of the integral control
   system. This includes the IMU, battery and the SD card.

### 3.3 Usability Requirements

The usability requirements should enable any individual from the wider
rocketry community to launch and operate the rocket and its accompanying
avionics package with relative ease. To ensure this, all hardware and
computer interaction stemming from the package's use cases must be
assessed against various heuristics.

#### Scenarios and Use Cases

##### Usability: Transporting

The rocket should feature the following properties to make it portable
and easy to transport:

- Contained within a single kit.
- Weigh no more than 1.5kg as per the NZCAA regulations \[2]
- Possess reasonable dimensions (must fit within a 29mm airframe as per
  the hardware requirements)

##### Usability: Base Station Setup and Interactivity

Prior to commencing the launch sequence, the rocket needs to establish a
connection with the base station module. The base station module
consists of a laptop and LoRa receiver to transmit commands and queries
as well as receive data. Base station setup should take 5 minutes
maximum.

##### Usability: Pre-Usability: Flight Tuning

The system needs to facilitate quick changes to the control system for
the different phases of flight, so that the flight characteristics can
better meet those required for a specific launch. This pre-flight tuning
interface should be in the form of a basic input/output system to
minimize the time required to make changes. **It is crucial that user
input is validated** to prevent the system from entering an incorrect
state.

##### Usability: Launch

During launch, the usability of the system should be centered around
reliability and safety. The rocket should feature the following features
to ensure this:

- The rocket should feature manual ignition to minimize the risk of
  premature ignition
- Ignition system should feature at least a 10m wire from the motor of
  the rocket to ensure the safety of the person igniting the rocket
- Launch critical features of the rocket are clearly marked and labeled
  for easy identification
- Hardware features to help mitigate the risk of incorrect operation of
  product, such as incorrect battery polarity.
- Software safety checks and pre-flight diagnostics to ensure all
  systems are operational
- Setting up the rocket should take no more than 15 minutes

##### Usability: Mid-Flight Diagnostics/Readings

During the flight, the system should:

- Broadcast telemetry at regular intervals to the base station to enable
  stakeholders manning the base station to monitor the flight in
  real-time
- Store readings into the on-board SD card to enable project
  stakeholders to analyze the performance of the rocket throughout the
  entire flight.
- Log all data on the base station in a readable format
- Log data at a sufficient resolution and sampling rate so that users
  are able to identify, any potential sources of issues.

##### Usability: Recoverability

The rocket needs to remain in working condition post-flight. This is
largely achieved through the use of a parachute system which is deployed
once the barometer detects an increase in air pressure. The user can
also specify a timer which will automatically deploy the parachute in
the event the barometer system fails.

##### Usability: Post-Flight Diagnostics/Analysis

At the end of a launch, the rocket should be in a state that enables the
project team and stakeholders to evaluate the performance of the rocket.
To allow this, the system should do the following:

- On-board SD card should be stored in an easily accessible part of the
  rocket to allow for quick installation and removal
- On-board SD card should be protected to withstand high velocities or
  hard impacts
- Broadcast mid-flight telemetry data should be stored onto a file at
  the base station's laptop as a backup to the SD card
- Disassembly of the rocket should take no longer than 15 minutes

##### Usability: Future Development

The purpose of the project is to contribute to the existing body of
knowledge about rocketry. To make the project usable by members of the
wider rocketry community the project requires:

- Documentation in the form of manuals
- Readable code
- Open source software available to the public.

### 3.4 Performance requirements

This section details the specific performance requirements that the user
can expect from the finished rocket.

The avionics package is expected to be capable of polling the onboard
IMU at least 100 times per second. This is important for the active
control aspect of the rocket. Due to the high velocity of the rocket,
the onboard microcontroller requires frequent input signals from the IMU
in order to make timely adjustments to the motor's vector in order for
the rocket to achieve an optimal flight path. If the IMU was polled at a
slower frequency the microcontroller would not receive sufficient
information regarding its current velocity and could overcompensate for
slight deviations resulting in stability issues. In addition to
providing active control of the rocket, the avionics package should
store these measurements at the same frequency on an SD card. These
measurements will also be supplemented by readings of the batteries'
voltage and current at a frequency of 10 measurements per second to
provide sufficient data to the user for post flight analysis.

Assessing the flight path, the rocket should be capable of consistently
achieving an apogee greater than 4 metres above the launch pad. The
rocket should also land with a horizontal displacement no greater than
25 metres to reduce the risk of people being injured or property being
damaged.

The GPS should provide accurate readings to within a five metre radius
of the rocket. This is to ensure that in the event that the rocket's
landing position is not immediately known, the GPS is able to provide
effective assistance in locating the rocket. In addition to this, the
rocket's radio unit is expected to achieve reliable connection to the
base station at distances of up to 80 metres without line of sight. This
is so that the GPS location can be successfully broadcast to the base
station even when environmental features obstruct vision.

In terms of durability, the rocket's design is required to be robust
enough to remain fully functioning following 10 individual launches.
This requires the rocket's onboard electronics, software and body to be
designed in such a way that ensures it is capable of enduring
accelerations in excess of 120 metres per second per second. This is an
important factor as the rocket's target demographic is the budget
conscious hobbyist. It also ensures, that the user is able to tune the
rocket over multiple consecutive launches to their preference.

### 3.5 Logical database requirements

This section outlines the software system that will be implemented for
the rocket.

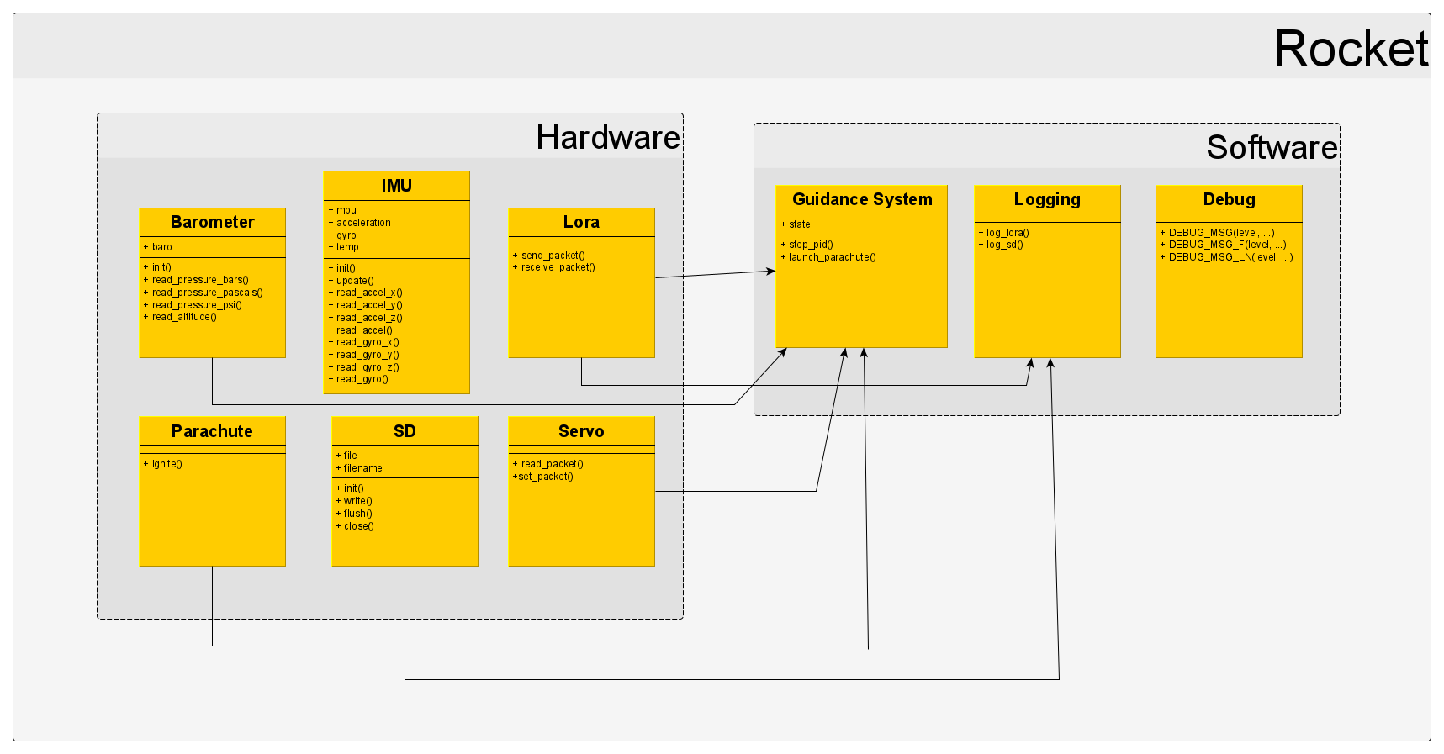
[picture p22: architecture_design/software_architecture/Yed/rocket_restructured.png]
UML Class Diagram


The software system is split into 2 main parts - Hardware, and Software.

**Please refer to section 4.1 of the [architecture document](../architecture_design/architecture-design.md/)
for technical details of the software system's implementation.**

### 3.6 Design constraints

#### 3.6.1 Hardware Design Constraints

For this project, the hardware design constraints are restrictions
imposed upon the rocket being built. The primary source of these
restrictions will come from legal requirements, given that the client
has specified only a single design constraint and has granted the
project team more freedom regarding the hardware design.

##### Physical Construction of the Rocket

According to the New Zealand Rocketry Association \[1], the physical
construction of a rocket with a motor class ranging from A-F must adhere
to the following rules:

- The rocket's body, nose, and fins are made of lightweight, non-metal
  parts only. The following materials have been approved:
  - Paper
  - Wood
  - Rubber
  - Plastic
  - Fiberglass
- The motor used must be commercially manufactured and certified.
- The rocket must be ignited through an electric ignition system with
  electric motor igniters with a removable safety interlock.
- The rocket cannot contain more than 125g of propellant.
- The rocket must not weight more than 1500g at lift off.
- The rocket cannot produce more than 320 Ns of total impulse.
- The rocket must have a recovery system in the form of a streamer, or a
  parachute, so it can land safely.
- Recovery wadding used must be fire-resistant or fire-proof.
- The rocket must not contain any payload that is intentionally
  flammable or could cause harm.

The rocket must also conform to regulation 9 of the Radio communications
Regulations 2001\[5]\[6]. Regulation 9 defines the available frequencies
for broadcast on a general user radio licence, it also specifies the
maximum broadcast power in dBW (Decibel Watts). We must also ensure that
we choose to broadcast on a frequency that doesn't have heavy traffic to
reduce the potential for interference.

In addition to these regulations, the client has specifically stated the
following hardware design constraint:

- The airframe's diameter must not exceed 29mm (preferably, the airframe
  is less than 29mm for usability and cost-effective purposes)
- The rocket must use the QFN package type for any integrated chips it
  uses.

#### 3.6.2 Software Design Constraints

##### Open Source Software

The client has clearly specified that the final result of the project is
intended to contribute to the existing body of knowledge available to
the rocket enthusiasts. The best way to ensure that this requirement is
met is by making sure that the software produced by the project is open
source and can be freely accessed by anyone. The open source nature of
our software introduces some constraints, one of which is that the
software produced during the project **cannot use non-open source 3rd
party libraries**. This limits the number of libraries that can be
utilized for the development of the software. Furthermore, the 3rd party
libraries that are used must not have any transitive dependencies with
other libraries that are not open source.

### 3.7 Nonfunctional system attributes

#### 3.7.1 Hardware Non-Functional System Attributes

##### Accessibility

The client has outlined that in previous iterations of this project, the
final product had issues with the accessibility of the physical rocket
hardware. It is imperative these issues are resolved as the client has
outlined that one of the purposes of this project is to contribute to
the wider rocket building community. Accessibility of the rocket in this
context means that the rocket will be relatively easy to assessable and
disassemble before and after launches. There must also be easy access to
all external interfaces on the rocket, including but not limited to:

- Power switch
- Launch safety interlock switch
- USB port for programming
- SD card
- Battery connector
- Parachute deployment charges

##### Reliability

It is crucial the hardware of the rocket is reliable as we are dealing
with potentially dangerous and harmful equipment. It was also specified
by the client that the hardware should retain its physical integrity when performing
simple actions incorrectly, like plugging in the battery or the sensors into the
main-board in the wrong orientation. Therefore, the reliability and accuracy of
components needs to be measured via testing to ensure that incorrect use
of certain components will not damage the hardware, or harm the user. To
protect the hardware, components such as sensors can be attached through
non-reversible connectors, or directly connected to the main-board of
the rocket. We can also ensure that all power systems are connected to
the main-board with non-reversible connectors, and that there are
reverse polarity protections present on the board.

#### 3.7.2 Software Non-Functional System Attributes

##### Correctness and Reliability

The client has highlighted that past attempts at the project by other
teams had issues regarding the correctness and reliability of the
software. This is especially important given that the project itself has
elements that are potentially dangerous. This means it is paramount that
the software works correctly and reliably. To assure the correctness of
the software, the project team will continually discuss what is defined
as correct behaviour as the project enters the execution phase. The
software will be packaged with extensive unit testing suites to prove
that the software is performing as intended. Continuous integration
testing will be setup in the GitLab repository of the project to ensure
that features merged during production do not cause errors with the
existing code base. From a coding perspective, the developers of the
software should apply programming techniques such as error handling,
pre/post condition checking and maintenance of invariants. Observing
these techniques should mitigate the risk of the software entering an
incorrect state and help ensure correctness and reliability.

##### Maintainability and Extensibility

Since the client has outlined that one of the purposes of the project is
to contribute to the wider rocket community, the software developed for
the project should be easily maintainable and extensible. This is
important since these attributes of maintainability and extensibility
should facilitate easier contribution to the project by other
individuals of the wider rocketry community. To achieve good
maintainability, the software needs to follow existing coding
conventions. Any 3rd party dependencies introduced to the software
should be well-known, easily adaptable, and adheres to a standard of
quality and usefulness agreed upon by the project team. From a lower
level perspective, maintainability can be achieved by observing the
'low-coupling, high cohesion' relationship between the different modules
of the software system. Extensibility can also be achieved by using
these techniques and is therefore important if the software is to be
added to or improved upon by other individuals after the completion of
the project.

##### Testing

Testing is crucial in the process of asserting the correctness and
reliability of the software. The testing strategy the project team will
adopt is a combination of regular unit testing and integration testing.
Unit testing will cover technical, lower-level aspects of the software
to ensure that the logic is correct. Unit testing should become a
regular part of the developer's workflow by running the unit tests
before pushing changes to the remote repository. Integration testing
will be accommodated by GitLab's CI/CD (Continuous
Integration/Continuous Delivery) feature. This will assist in ensuring
that code being merged into production meshes well with the existing
code base.

Other non-functional requirements from a software perspective include
the following:

- **Documentation** - The software package should have comprehensive
  documentation to clearly convey the intent and purpose of the code.
- **Code Quality** - The software should adhere to existing coding
  conventions and follow design patterns where appropriate. The software
  should facilitate easy maintenance and adaptability.
- **Ease of Deployment** - Deployment of the software system should be
  easy for the user. A manual should accompany the software to describe
  how to use it, and to describe any important parts of the software the
  user should be made aware of.

### 3.8 Physical and Environmental Requirements

#### 3.8.1 Physical Requirements

The physical requirments placed on the rocket stem from the physical
constraints imparted by the local authority and the client's minimum
viable product. The requirements are:

- Dimensions: The rocket will be of cylindrical shape with a nose at the
  top and gimbal at the bottom. The airframe will be 29mm in diameter
  and approximately 125mm in length. The nose cone at it's base is 30mm
  and 50mm in height. The gimbal spans 50mm in diameter and 60mm in
  height.

- Mass: Excluding the d class motor is 80g and 124.5g inclusive.

- Material: The rocket will be constructed largely from plastic
  including 3D printed parts.

The components need to be sourced from well-known NZ suppliers. In this
project most of the parts are sourced from DigiKey. Additional parts
left from the previous 2018 team are also utilised to reduce cost and
risk of part failure. These components are assembled and tested at
Victoria University of Wellington inside a laboratory. The physical
parts used in the design are:

- D-class motor: Solid fuel rocket motor supplying ~20Ns of thrust over
  2 second window.

- Adafruit Feather STM32F405: On-board microcontroller for implementing
  the active control system, communications and processing sensor data.

- MPU-6050: The IMU for providing data regarding position and momentum
  of the rocket to the microcontroller.

- Adafruit RFM96W: LoRa radio trancievers for establishing remote
  communication between the microcontroller and base station.

- Adafruit Mini GPS PA1010D: GPS module for providing positional data to
  the microcontroller.

- Secondary microcontroller for interfacing between the basestation
  laptop and LoRa trancievers.

A custom PCB design is implemented to reduce the size of the electronics
making it possible for them to fit inside the 29mm airframe. Programming
of the device is achieved by flashing via micro usb.

#### 3.8.2 Environmental Requirements

The environmental requirements are based primarily around legal
restrictions and safety requirements. According to the New Zealand
Rocketry Association \[1], a rocket with a motor class ranging from A-F
can only be launched under the following environmental circumstances:

- Wind speeds at the site of the launch do not exceed 32km/h
- No dry grass must be present near the launching location of the rocket
- People must maintain at least 5m distance from the rocket during a
  launch

In addition to the guidelines provided by the New Zealand Rocketry
Association, the New Zealand Civil Aviation Authority (NZCAA) Rules Part
101.15 \[2] places the following restrictions:

- A rocket cannot be operate on or within 4km of an aerodrome boundary
  unless permission is given by the aerodrome operator
  - If permission is granted, the rocket still has the following
    environmental restrictions:
    - The rocket cannot fly above 400 feet (121.92m) AGL (Height above
      ground level)
    - The rocket cannot interfere with the flight path of any aircraft
    - The rocket cannot be operated over an active runway
- A rocket cannot be operated within 4km to 8km of an aerodrome boundary
  if it exceeds an altitude of 400 feet AGL.
- A rocket cannot be launched in an environment where clouds or other
  obscuring meteorological phenomena has a substantial presence
- A rocket cannot be launched if horizontal visibility is less than 8km
- Rockets cannot be launched at night under any circumstance

### 3.9 Supporting information

#### Open Source

The client has communicated that their intention with the project after
its completion is to contribute to the wider rocketry community. As a
result, all of the project's content including hardware design and
source code will be freely available to the public both for viewing and
editing. This is an important factor in the design of the hardware and
software systems since it imposes certain restrictions that the project
team has to work around. Despite these restrictions, making the project
open source allows the project to be improved upon by other individuals
outside of the project team, and hopefully, provoke continued interest
for the wider rocketry community.

##### Legal Regulations

The project is subject to a wide range of legal regulations given the
potentially dangerous nature of the product being developed. **It is
critical that all legal regulations are followed by the design** of the
system as any breaches can pose a real threat to the health and safety
of project stakeholders. Furthermore, the legal repercussions from any
breaches could severely impact the project and its ability to continue.

## 4. Verification

This section outlines how specific requirements of the avionics package
will be verified. Where possible this includes testable and measurable
acceptance criteria.

### 4.1 External Interfaces

The requirements for assessing whether the individual external
interfaces have met their requirements are specified below.

#### Interface: Radio Antenna

For the radio antenna to be verified it must meet the following
criteria. The radio antenna upon request from the base station should be
able to transmit the geographical location data and be received at the
base station without error. The radio antenna must also have the
capacity to receive and respond to three distinct commands and provide
live telemetry of at least one flight critical variable during flight.

#### Interface: SD Card

The SD card storage will be deemed satisfactory if it can in any
capacity store data provided by the IMU and GPS during flight in a
format that can be interpreted by the user later. As long as the data
can be read and does not contain corrupted data, it will be verified.

#### Interface: Internal Measurement Unit (IMU / Sensors)

The onboard IMU will be verified, provided that it is able to reliably
produce data throughout the duration of the flight. The data must also
match the observed flight path of the rocket to a reasonable extent.

#### Interface: Guidance System

In order to verify the guidance system, software testing of the
controller must produce evidence that the guidance system is able to
offset/correct to any given extent three consecutive deviations in the
simulated flight of the rocket.

#### Interface: Gimbal

The Gimbal can be verified granted that it is able to vector the rocket
motor on two axis and is observed to change the motors vector at least
once during flight.

#### Interface: GPS

The GPS will be verified if and only if following the flight of the
rocket, the geographical location data produced by the unit is accurate
to within a 5 metre radius of the rocket.

### 4.2 Functions

#### 4.2.1 Verifying Use Cases

1. Launching the rocket: This use case is verified if project
   stakeholders are able to launch the rocket safely through manual
   ignition.
2. Transportation of Rocket: This use case is verified if the rocket is
   able to be transported from one location to another safely. Any
   stakeholder should be able to transport the rocket with relative ease
   unless the rocket is in a state of being susceptible to ignition, in
   which case a professional or experienced stakeholder can transport
   the rocket safely.
3. Assembly of Rocket: This use case is verified if the rocket is able
   to be assembled within 15 minutes.
4. Disassembly of Rocket This use case is verified if components of the
   rocket are able to be removed in order to be replaced.
5. Reading of Flight Data: This use case is verified if the rocket
   successfully transmits critical telemetry data to the base station
   during launch and its flight to enable project stakeholders to
   monitor the flight.
6. Analysis of Flight Data: This use case is verified if the broadcast
   telemetry data is recorded and stored in a way that enables the
   project stakeholders to analyse the flight.

#### 4.2.2 Verifying Requirements

1. Rocket is safe to transport: This requirement is verified if the
   rocket can be held and taken from one location to another with full
   assurance that it is of no danger to any person or property. The only
   exception to where it should not be safe to transport is during
   launch.
2. Rocket is re-usable: Reusability of the rocket is verified if the
   rocket does not sustain significant physical damage after a flight,
   and that a recovery system in the form of a parachute or streamer
   \[2] is implemented to ensure this.

3. System enables post-flight analysis: This requirement is verified if
   the system has a way of sensing, recording and broadcasting telemetry
   data during launch and flight. The system should log this data to
   both an on-board SD card, and the base station. The verification of
   this requirement will fail if **both** of the platforms logged to by
   the rocket (on-board SD card and base station) cannot display the
   logged data due to some failure.
4. Rocket is tunable for optimisation: This will be verified provided an
   interface exists in which the user can modify the flight parameters
   while out in the field.
5. Rocket can be launched 15 minutes after flashing: This requirement is
   verified if the assembly process of the rocket takes no longer than
   15 minutes.
6. Rocket consists of a single kit: This requirement is verified if all
   components required to assemble the rocket are small enough to fit
   into a suitable sized container.

**_Hardware_**

1. Withstanding significant acceleration: The rocket and its components
   must be able to withstand at least 20ms<sup>-2</sup> of acceleration
   during its flight in order for this requirement to be verified. If
   components are unintentionally separated from the rocket, or is
   dislodged from its intended position within the rocket, this
   requirement will fail to meet the verification standards. Verifying
   this requirement can be achieved by ensuring secure mounting of
   components within the rocket.
2. Safe Landing: This requirement is verified if the rocket is able to
   perform a safe and slow landing as a result of deploying a recovery
   system after a set amount of time during its flight. Alternatively,
   the parachute is deployed when the on-board barometer detects an
   increase in air pressure, accompanied by a deceleration as indicated
   by the IMU. A landing that causes noticeable damage to any person or
   property despite the deployment of the recovery system will mean that
   this requirement will fail to meet the verification standard.
3. Fits within an enclosure with the specified dimensions - This requirement is verified if the
   entire rocket posses a width and diameter of no more than 220mm by
   50mm respectively. The comnponents must also fit within an airframe
   whose maximum width does not exceed 29mm. Exceeding any of the
   specified dimensions fails the verification of this requirement.
4. Open Source and Accessible: This requirement is verified if all work
   contributing to the development of the hardware system of the rocket
   is openly visible to the public, and that the total cost of all
   components is less than or equal to \$300 NZD. To verify this
   requirement, all schematics, plans and diagrams related to the
   hardware system of the rocket will be available on GitLab. Tools used
   to create schematics, plans and diagrams will be open source, or free
   to use.

**_Software_**

1. Error Correction and Control: This requirement is verified if the
   software system correctly guides the rocket to take a safe, upward
   trajectory despite the influence of external factors such as wind
   speed and direction. The software system must use a combination of
   internal sensor readings on-board the rocket, as well as data
   provided by the mission control software.
2. Logging: This requirement is verified if the software system
   successfully logs important data from the IMU, Radio and GPS to both
   an on-board SD card and base station during flight. The logged
   information must be accessible post flight, otherwise this
   requirement is not verified. This can be verified by creating a
   dedicated Logger module that logs important data to target components
   (on-board SD card and base station) during the flight at a sufficient
   rate to be useful.
3. Mid-Flight Error Analysis: This requirement is verified if the rocket
   responds to erroneous data in a way that does not cause the rocket to
   fail, or enter a state where it can no longer be trusted to take a
   safe trajectory. This requirement can be verified by conducting
   extensive software testing.

### 4.3 Usability Requirements

The usability of the rocket revolves around the idea of how the user
will interact with the system to achieve important use cases, and how
easy this is to do. To verify the usability requirements, each important
scenario/use case must have a set of criteria that must be met to
indicate that the usability of the system under that scenario has been
verified.

#### Verification Under Specific Scenarios

The following criteria specifies what must be done for each important
use case/scenario in order to verify the usability of the system.

##### Transporting

- The final version of the rocket is contained within a **single
  physical construct or kit**.
- The total weight of the final rocket and its components weigh less
  than or equal to **1.5kg** \[2].
- At its widest point, the rocket's airframe has a diameter of less than
  or equal to 29mm.

##### Base Station Setup and Interactivity

- The setup of the base station laptop, USB LoRa, and the software
  module to enable interaction between the rocket and the base station
  takes no longer than **5 minutes to setup.**

##### Pre-Flight Tuning

- A basic, intuitive input/feedback system is implemented.
- User input is validated.
- Useful **feedback** is provided to the user if invalid input is
  detected.

##### Launch

- The stakeholders are able to perform a successful launch at a safe
  distance from the rocket.
- Manual ignition is featured as the primary ignition method to assure
  the safety of the stakeholders.
- Launch critical features are easily identified by stakeholders or by
  people who are unfamiliar with the rocket as a result of effective
  marking and labelling.
- The rocket can be assembled by stakeholders in under **15 minutes**.

##### Mid-Flight Diagnostics/Readings

- Stakeholders can easily read the logged .
- Stakeholders manning the base station can make confident deductions
  about the flight as a result of a sufficient logging rate and format.

##### Recoverability

- A parachute system is deployed to enable the rocket to land safely.
- GPS system is accurate to within **5 m** of the rocket's landing site
  to enable project stakeholders to quickly locate the rocket upon
  landing.

##### Post-Flight Diagnostics/Analysis

- Stakeholders are able to retrieve the on-board SD card without the
  need to fully disassemble the rocket.
- On-board SD card is intact at the end of the flight.
- Rocket disassembly takes no more than **15 minutes**.

##### Future Development

- Documentation in the form of manuals are written to enable any
  potential user to understand the system quickly.
- Software is documented appropriately to **support the ability of
  future contributors to adapt the code**.
- The project is open source so any future contributors can easily
  access the project.

### 4.4 Performance Requirements

#### In-Flight Verification

The avionics package will have met the performance requirements provided
the rocket maintains a flight trajectory of no more than 90 degrees from
the vertical while the motor is still producing thrust. This is evidence
that the onboard controller provided sufficiently accurate and
well-timed signals to the gimbal in order to achieve controlled flight.
If the rocket deviates from the vertical by greater than 90 degrees, the
avionics package will not have met the performance requirements. In
addition to this the avionics package must achieve an apogee of at least
1 meter, and a horizontal displacement upon landing of less 25 metres to
be verified.

The avionics package must also have in some capacity, stored data
collected from the onboard IMU and GPS during flight to be verified.

#### Physical Attribute Verification

Lastly, the avionics are required to be able to perform two consecutive
launches. This provides evidence that the package is capable of
completing a launch and being recovered in working condition. Minor
damage, that is damage requiring no spare parts and less than 30 minutes
of attention to fix, is permitted. If the package fails to meet this
requirement it is evidence that its physical attributes were not
acceptable and hence the package cannot be verified.

### 4.5 Logical Database Requirements

The logical database requirements are focused around the idea of how the
software developed will be laid out, as well as the connections and
dependencies that exist between the software modules to enable each
other's functionality. This is verified as a whole if the final software
system achieves the core functionality outlined in each of the software
modules, but still retaining overall architecture of the system. This
means that the separation of duties must be enforced as the software
system is developed. By doing this, the software system will achieve
high cohesion, maintainability and good modularity.

To verify these requirements, the developers of the software system
should make a conscious effort to become familiar with the desired
architecture of the software system and the different modules that needs
to be implemented before coding it. The project team should regularly
consider if changes can be made to the logical database requirements
that will have a beneficial impact to the software system.

The logical database requirements will fail to meet verification
standards if the software system's architecture has deteriorated beyond
recognition. This can potentially happen due to poor execution and
failure to follow the outlined software architecture/layout as outlined
in section 3.5.

### 4.6 Design Constraints

#### 4.6.1 Verifying Hardware Design Constraints

The hardware design constraints of the project will have been satisfied
if the final rocket's properties abide by both legal regulations \[2],
and the client's hardware constraints.

For the legal regulations, the hardware design constraints are satisfied
if:

- The rocket weighs less than or equal to 1.5kg at liftoff
- The rocket contains no more than 125g of propellant
- The rocket's body is composed of non-metal materials
- The rocket has a recovery system in the form of a streamer or
  parachute
- The rocket's motor is manufactured by a certified company.
- The rocket must be manually ignited through an electric ignition
  system

The client has provided only a single hardware design constraint: The
rocket's airframe must not exceed a diameter of 29mm. This hardware
design constraint is satisfied if the diameter of the rocket's body is
less than or equal to 29mm, although preferably less than 29mm for
transportability, aerodynamics, and cost-efficiency purposes. To ensure
that these hardware design constraints are met, the project team will
consult these design constraints regularly during the execution phase of
the project. It is important to note that the majority of the hardware
constraints are sourced from legal regulations in accordance with the
NZCAA \[2]. As a result, the team will closely monitor if any changes to
the legal regulations occur and update the design constraints as
necessary to make sure that the hardware design constraints are verified
at the end of the project.

#### 4.6.2 Verifying Software Design Constraints

One of the primary software design constraints that needs to be verified
is whether the software is open source and hence whether all 3rd party
libraries/APIs are also open source. To satisfy this constraint, each
3rd party library the project team elects to use must be open source.
This can be achieved by making sure that the library/API is licensed
under a license that is consistent with those outlined by the Open
Source Initiative \[4]. Such licenses include the following but are not
limited to:

- Apache License 2.0
- MIT License
- GNU General Public License (GPL)
- BSD-3 Clause ("New" or "Revised" License)

Transitive dependencies (other libraries/APIs used by the 3rd party
library/API) must also be open source. If this is not the case, then the
project will fail to meet the open source software design constraint of
the project.

### 4.7 Nonfunctional System Attributes

#### 4.7.1 Verifying Hardware Non-Functional System Attributes

**Attribute 1 - Accessibility**:

The client has specified that previous attempts at the physical design
of the rocket suffered from accessibility issues. As a result, it is
important that the rocket is built to facilitate easy access to its
components. This non-functional requirement is verified if the client
can make the assessment that all external interfaces on the rocket are
accessible with minimal effort.

**Attribute 2 - Reliability**:

The verification of this attribute will rely on the fact that the rocket
and its components does not sustain any significant damage during normal
use. The rocket is considered reliable if it is able to undertake
several flights, and is constructed in a way that prevents physical
damage to its components. This also requires that the package
consistently meets the design requirements and functionailty without
issue.

#### 4.7.2 Verifying Software Non-Functional System Attributes

**Attribute 1 - Correctness and Reliability**:

The verification of this attribute requires a large amount of testing.
Verifying the correctness and reliability of the software system can be
achieved through rigorous unit testing to verify the lower level logic
of the code. Unit testing will be conducted on _all_ software modules to
verify the overall correctness and reliability of the software.
Furthermore, unit testing will be integrated into the regular workflow
of the team. This means that at every sprint, a set of test cases will
be formed, which the target software module must pass at the end of the
sprint. For software tests that require the usage of hardware components
or a fully/partially built rocket, testing will be conducted in a highly
controlled environment where the project team has full control over what
happens to the components, and the outcome is known. This attribute is
verified if the software performs as intended and is deemed as
sufficient by the project team, and the client.

**Attribute 2 - Maintainability and Extensibility**:

To verify this attribute, the project team members in charge of
developing the software must be in **full agreement** that relevant
programming techniques that promote maintainable and extensible design
were observed to the best ability of the developers. Some of the
programming techniques that can facilitate maintainable and extensible
software include the following but are not limited to:

- Observing low coupling - high cohesion where appropriate
- Adhering to existing coding conventions
- Commenting
- Proper usage of abstraction
- Observing 'DRY' (Do not repeat yourself)
- Formal documentation in the form of comments and/or API manuals

Furthermore, personas will also be used in the verification process of
this attribute. Each persona will be considered to see if that persona
can understand the code-base and the manuals provided in a way that will
enable them to make suggestions or apply changes to the code.

**Attribute 3 - Testing**:

This attribute can be verified by assessing the package against
quantitative and qualitative metrics. From a quantitative point of view,
this attribute is verified if the following conditions are met:

- 90% overall code coverage is achieved by all unit tests
- A quota of 25 unit testing methods are achieved by the end of the
  project

From a qualitative point of view, this attribute is verified if the
following conditions are met:

- All tests pass across all software modules by the end of the project
- Test cases written for a specific software module should lead to the
  software module working as expected. This will indicate that the tests
  are valid.
- A wide range of potential cases are covered, including valid, invalid
  and edge cases
- Gitlab's CI/CD feature is used appropriately to facilitate system and
  integration testing

Note that Attribute 1 (Correctness and Reliability) depends heavily on
this attribute. It is important that the verification of this attribute
is achieved, and done so comprehensively, given the potentially
dangerous nature of the product being developed by the project.

### 4.8 Physical and Environmental Verification

The physical requirements placed on the rocket can be verified provided
that:

- The rocket's airframe is less than 29mm in diameter.
- The overall dimensions do not exceed 220mm in length and 50mm in
  diameter.
- The mass of the rocket does not exceed 1.5kg.
- The rocket is small enough to fit inside of a portable container.

The environmental requirements can be verified given:

- The environmental conditions meet the requirements of the New Zealand
  Rocketry Association \[1] which specify:

- The environmental conditions adhere to the New Zealand Civil Aviation
  Authority Rules Part 101 \[2] which specify:

- The rocket adheres to the guidelines presented by the Faculty of
  Engineering and Computer Science at Victoria University which will be
  checked at all times throughout the duration of the project.

- The rocket is launched at a location permitted by the Wellington City
  Council and does not damage the surrounding property or the environment.

## 5. Development schedule

### 5.1 Schedule

**Architectural Prototype** Completed by June 19th.

**Minimum Viable Product** Completed by September 11th.

**Further Releases** Final prototype due, as well as any other planned
significant releases. Published by October 18th.

### 5.2 Budget

In total the project has an allocated budget of \$300.00 NZD.

Presented here is a table outlining the expenditure on key components.
All links and prices valid as of the 15th of June 2020.

| COMPONENT | COST | NAME/DESCRIPTION/LINK | REASONS FOR CHOICE |
| :--- | :--- | :--- | :--- |
| Micro-Controller | \$24.95 USD | Adafruit Feather STM32F405 (168MHz) [BUY](https://www.adafruit.com/product/4382), [Github](https://github.com/adafruit/Adafruit-Feather-STM32F405-Express-PCB), [Documentation](https://www.digikey.co.nz/en/videos/a/adafruit/programming-the-adafruit-feather-stm32f405-express-with-stm32cubeide-maker-io) | Small, Light, Good Opensource Libraries & Good Documentation |
| IMU | \$17.59 NZD | BNO055 [BUY](https://nz.mouser.com/ProductDetail/Bosch-Sensortec/BNO055?qs=QhAb4EtQfbV8Z2YmISucWw%3D%3D), [Datasheet](https://nz.mouser.com/datasheet/2/783/BST-BNO055-DS000-1509603.pdf), [Adafruit library](https://learn.adafruit.com/adafruit-bno055-absolute-orientation-sensor/arduino-code) | Good Libraries, quaternions, Better Documentation |
| GPS | \$61.93 NZD | Adafruit Mini GPS PA1010D [BUY](https://www.digikey.co.nz/products/en?keywords=PA1010D), [Datasheet](https://cdn.taoglas.com/datasheets/GP.1575.25.4.A.02.pdf) | Cheap, Small and Meets requirments |
| Transceivers | \$19.95 USD | Adafruit RFM96W LoRa Radio Transceiver Breakout - 433 MHz - RadioFruit [BUY](https://www.adafruit.com/product/3073), [Overview](https://learn.adafruit.com/adafruit-rfm69hcw-and-rfm96-rfm95-rfm98-lora-packet-padio-breakouts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), [Datasheet](https://cdn-learn.adafruit.com/downloads/pdf/adafruit-rfm69hcw-and-rfm96-rfm95-rfm98-lora-packet-padio-breakouts.pdf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) | SPI, Pins for extra antenna |
| Gimbal Servos | \$6.97 NZD each | SERVOMOTOR RC 6V MICR METAL GEAR [BUY](https://www.digikey.com/product-detail/en/dfrobot/SER0011/1738-1232-ND/7087129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) | 15grams Small, Cheap, Has dimension specifications |
| Battery | \$12 NZD | ZIPPY Compact 500mAh 2S 35C Lipo Pack [Buy](https://hobbyking.com/en_us/zippy-compact-500mah-2s-35c-lipo-pack.html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) | -Available in Australia, - Sufficient Charge, Voltage and Current discharge specifications, - Cheap, -Light for a battery |
| Power supply | \$3.62 USD | See power_supply.md | See power_supply.md |
| - | ~ \$230 NZD | - | - |

### 5.3 Risks

The content below outlines the 10 most important risks that threaten the
completion of the project goals. Attributes of each risk such as the
likelihood of occurrance and extent of impact are described as follows:

- Likelihood: - Unlikely, Likely, Very Likely
- Impact - Mild, Moderate, Severe

**Risk 1 - Rocket falls on a person causing injury**:

- **Risk Type:** Health and Safety
- **Likelihood:** Unlikely
- **Impact:** Severe
- **Mitigation Strategy:** During a rocket launch, all attending project
  members and other stakeholders/spectators are required to maintain a
  safe distance from the rocket. Any member of the public present at the
  launch site will be informed of the rocket launch so that they are
  made aware of the potential danger. During the rocket's flight, the
  trajectory and status of the rocket will be closely monitored to
  ascertain the landing location of the rocket. If there are too many
  people at the launch site, the launch will be postponed. Ensure that a
  recovery system in the form of a streamer or parachute is implemented
  \[1] to minimize the damage done by an impact with a person during
  landing. Project stakeholders involved with the rocket launch will
  maintain a minimum distance of 5m from the rocket during a launch, as
  required by the NZRA \[1].

**Risk 2 - Rocket contacts object causing damage**:

- **Description:** Rocket unintentionally makes contact with an object
  during flight or when it lands, causing damage to property
- **Risk Type:** Health and Safety, Environmental
- **Likelihood:** Unlikely
- **Impact:** Moderate
- **Mitigation Strategy:** The site of the rocket launch will be
  inspected closely prior to the launch to determine if there are any
  objects belonging to the project members or to the members of the
  public. The location of the launch site must be a safe distance away
  from any buildings, cars and roads. Ensure that a parachute deployment
  system is implemented to minimize the damage done by an impact with an
  object during landing.
- One potential mitigation strategy is to limit the altitude the rocket
  can reach. Customer specifically said that the priority of the project
  is control and that the rocket reaching high altitudes is not the goal
  or desired. This mitigation strategy can also apply to Risk 1.

**Risk 3 - Rocket takes unsafe path due to wind causing damage**:

- **Description:** Rocket's trajectory affected by winds, causing it to
  take an unsafe flight path causing injury or damge to property.
- **Risk Type:** Environmental
- **Likelihood:** Unlikely
- **Impact:** Severe
- **Mitigation Strategy:** Consult mission control software before a
  rocket launch to determine if the current wind speeds can safely
  accommodate a flight. Launches will be postponed if wind speeds exceed
  **32km/h** \[1].

**Risk 4 - Rocket disassembles during flight**:

- **Description:** Rocket parts unexpectedly disassembles during flight
  debris emitted causes damage to people and property.
- **Risk Type:** Health and Safety/Environmental
- **Likelihood:** Unlikely
- **Impact:** Moderate
- **Mitigation Strategy:** During assembly, team needs to ensure all
  components of the rocket are securely fastened. The design should
  ensure that the majority of components are contained within the
  airframe. Inspection of the assembly will be required prior to launch.

**Risk 5 - Covid-19 pandemic causes lock-down hindering progress**:

- **Risk Type:** Legal/Health and Safety/Environmental
- **Likelihood:** Very Likely
- **Impact:** Moderate
- **Mitigation Strategy:** The project team will continue to work
  remotely, using tools as specified in the team contract to maintain
  communication during the lock-down period. Hold meetings remotely as
  outlined in the team contract to continually assess and provoke
  progress. Focus of the project will shift to parts of the project that
  do not require the practical application of hardware. Hardware related
  components of the project will be simulated. Project members will
  closely monitor the situation and decide on the achievability of
  certain project objectives in a reactive manner.

**Risk 6 - Covid-19 pandemic affects global logistics**:

- **Description:** Covid-19 pandemic affects global logistics, making it
  difficult to procure equipment and parts.
- **Risk Type:** Resources
- **Likelihood:** Very Likely
- **Impact:** Moderate
- **Mitigation Strategy:** The project team will continue to plan and
  budget for the equipment and parts required so when the ability to
  order parts becomes feasible, the team is able to order such parts
  immediately and mitigate the time lost to progress with the project.
  The project team will discuss with the client if certain parts can be
  recycled from previous attempts at the project by other teams.

**Risk 7 - Rocket ignites prematurely causing injury to people**:

- **Risk Type:** Health and Safety
- **Likelihood:** Unlikely
- **Impact:** Severe
- **Mitigation Strategy:** At all times during a launch, project
  stakeholders involved with the launch must maintain a safe distance of
  at least 5m. Manual ignition system must be electric, and have a
  safety interlock in place \[1]. A first aid kit will be brought to the
  launch site to treat any minor injuries on site. A comprehensive
  physical interlock system will be implemented such that a conscious
  effort has to be made by a stakeholder to initiate a launch.

**Risk 8 - Rocket takes unsafe path due to software failure**:

- **Description:** Rocket takes an unsafe trajectory mid-flight due to
  software error, causing damage to people or objects.
- **Risk Type:** Health and Safety/Environmental
- **Likelihood:** Unlikely
- **Impact:** Severe
- **Mitigation Strategy:** The project team will extensively test the
  software to validate its correctness before proceeding with a rocket
  launch. An alert system implemented by the software will trigger to
  inform the relevant stakeholders of the impending situation so that
  stakeholders are able to act appropriately. This is a feature that
  came up during a meeting with the client, they stated that it would be
  a nice feature to have the ability to manually deploy the drogues in
  the event a situation like this happens.

**Risk 9 - Rocket ignition causes a fire**:

- **Risk Type:** Health and Safety/Environmental
- **Likelihood:** Unlikely
- **Impact:** Moderate
- **Mitigation Strategy:** Project stakeholders must undertake a health
  and safety induction prior to the launch In accordance with the NZCAA
  \[1], the selected launch site must be clear of dry grass to lower the
  risk of causing a fire during a rocket ignition. The project
  stakeholders involved with the launch will closely inspect the launch
  site for flammable material to remove them. A rocket launch will be
  postponed if the fire alert level is high, or if the temperature is
  unusually high. A fire extinguisher will be brought by the team at the
  launch site to counter small fires.

**Risk 10 - Sudden change in wind speed mid flight**:

- **Description:** Wind speeds suddenly exceed the safe wind speed for
  the rocket during flight
- **Risk Type:** Health and Safety, Environmental,
- **Likelihood:** Unlikely
- **Impact:** Moderate
- **Mitigation Strategy:** The rocket launch will only proceed if the
  current wind speeds are well below the maximum wind speed determined
  for the rocket. Wind speeds will be continually monitored during the
  flight to keep the team informed on the safety of the flight. Recovery
  system will be manually deployed in the event that the wind speed
  rises to an unsafe level.

### 5.4 Health and Safety

**1. Managing computer related risks**:

- It is the responsibility of the individual to make sure they have done
  the best they personally can to ensure they have a healthy, safe and
  tidy working environment. However, if for any circumstances these
  conditions cannot be met for an individual, there are still options
  that can be done as a team to ensure everyone's health and safety when
  undergoing computer related activities.
- In general, when it comes to computer usage, it isn't healthy to spend
  an inordinate amount of time in front of the screen. This often can be
  amplified by complications regarding the suitability of their working
  environment. If any team member feels they have an inadequate working
  environment or an excessive amount of work they have been assigned.
  Then their obligation is to let the rest of the team know of their
  situation. The importance of this is as a team, we all share common
  interests and goals for the project. In sharing their situation with
  the team, it is then the teams responsibility to reassess the full
  situation. The team will get together and discuss what they can do to
  lighten the burden off of the affected team member. This could be in
  the form of lightening the sum of work assigned to the individual.
  However, it might also look like changing the type of work assigned in
  order to meet the means of the affected individual. An example of this
  might be if a team member was tasked with a computationally demanding
  task that requires running a heavy simulation on their device. If the
  team member did not have access to a sufficiently powerful machine,
  then they are obliged to notify the team of their current situation.
  The team is then obliged to consider the members request and discuss
  rescheduling work appropriately. Another potential issue is whether
  the individual has a computer that is not physically compatible with
  the assigned tasks, or their device requires an exceptional amount of
  work to configure (software incompatible -> such as wrong operating
  system). What is considered physically incompatible may also be vague.
  For example, another interpretation of this might be, if a pending
  task requires creating large state diagrams (requiring a bigger
  monitor), and the team member only had access to a small laptop
  screen. The team member could ask for a reassessment of work such that
  they can find something that better suits their means.

**2. External Testing Sites**:

- In the event that the team decides to perform work or testing at any
  external (off-campus) workplaces/sites, it is paramount that
  appropriate considerations are made ahead of time. These
  considerations will be realised in the form of a health and safety
  plan. Before the team visits any planned locations, they must first as
  a group, brainstorm or discuss any health and safety risks that might
  be applicable to the location. It is important to note that mental
  health is also a vital consideration. Once these risks have been
  assessed, mitigation strategies can be developed to minimize the impact
  of these risks. If any individual has concerns conflicting with the
  team about any offsite locations, then they can
  either express their stance with the team, or discretely raise the
  concern with the course coordinator / health and safety officer. Any
  industrial locations must require an induction, whether this is
  official, or provided unofficially by a member with strong knowledge
  of the environment.

**3. Test Subjects and Ethics**:

- The team as a whole has stated that they have strong objections with
  any work or testing on any animal subjects. The scope of this project
  entails creating software and hardware for miniature model rockets
  strictly used for conventional hobby-like activities. In the unlikely
  event where the team becomes aware of the intention of either their
  software or hardware being used for unethical or extreme activities,
  then the team will halt any work until they have thoroughly assessed
  the situation. Should the intentions of the project usage, or scope
  change to an undesirable nature, then they have the right to halt all
  work undertaken indefinitely.

#### 5.4.1 Safety Plans

Please refer to the project's
[Safety Plan Analysis](https://gitlab.ecs.vuw.ac.nz/course-work/engr300/2020/group3/group-3/-/blob/72-proofread-requirements-doc/project_requirement/safety-plan-analysis.md)
document for further information.

## 6. Appendices

### 6.1 Assumptions and dependencies

- **Interaction with Mission Control Project** - A fully functioning avionics
  package relies on a reliable, fully developed mission control software
  provided by a separate team. This is due to the fact that the mission
  control software is responsible for monitoring the launch environment
  to determine whether or not the environment permits a safe launch. An
  agreed upon communications protocol between the rocket and mission
  control is required to enable the rocket to communicate between itself
  and mission control.

- **Interaction with Simulation Project** - The PID of the control system
  is too costly to test with real launches. This project assumes that the
  testing of the control system will be happening in a simulated
  environment, as facilitated by monte carlo software developed by a
  separate team.

### 6.2 Acronyms and abbreviations

IMU (Inertial Measurement Unit): A device capable of sensing forces acting
on a physical body.

CI/CD (Continuous Integration/Continunous Delivery): The software process
of merging version control branches into a single branch and conducting
software operations and workflow (i.e testing) in an automated fashion.

NZCAA (New Zealand Civil Aviation Authority): Governing body with regards to
aviation rules and procedures.

GPS (Global Positioning System): A device that tracks the position of the object
it is attached to in the world.

DRY (Do not repeat yourself): A software philosophy centered around reducing
redundancy and repetition in software systems.

---

## 7. Contributions

| Member | Contribution |
| :---: | :---: |
|  Niels Clayton | 3.1 - 3.2, 3.8.1, 5.2 |
|  Ron Crisostomo  | 2.0, 3.3, 3.6, 3.7.2, 3.8.2, 3.9, 4.3, 4.6, 4.7.2, 5.3, 6.0 |
| Will Fowler | 3.4, 4.1, 4.2, 4.4, 4.7.1, 4.8, 5.2 |
| Billy Robb | 1.1, 1.3.1, 1.3.2, 1.3.3, 1.3.4, 5.1, 5.2, |
| Finlay Sargisson | 1.2, 1.3.3, 3.2, 3.5 |
| Zac Scott | 3.2, 3.5, 5.4, Formatting, table of contents, |

---

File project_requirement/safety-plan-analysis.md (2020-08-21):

# Safety Plan Analysis

[[_TOC_]]

## Planning

> Zac Launch details, travel plans and environment subsections Finn:
> Front cover, and The rocket Will: Launch, unforeseen events, fault
> components and supervision.

## Analysis of 2018 safety plans

- disclaimer that it's only valid till first milestone
- Name
- Project Name
- Start and End Data
- Risk Profile
- The Highest risk in project

\[DRAFT]

## Safety Plan

Note: This Safety Plan is valid for the first milestone of the project.
***TODO: do we have a launch document?***

Name: Project Beans (Group 3) Project Name: Avionics and Control Project
Start Date: 17 March 2020 Project End Date: 16 November 2020

Risk profile of the project : Major

The most severe risk that this package entails is the rocket falling on
a person causing serious injury.

## Section 1 - The Rocket

> - maximum weight
> - maximum length
> - motor specs
> - OpenRocket for test simulations
>
> > - Results of the simulations - estimates/averages
> > - worst case scenario based on sims
>
> - no metal parts (complying with **NZ Model Rocketry Safety Code**)
> - ignition safety locks
> - **CAA requirements** of 20 Newtown-seconds impulse is not met so
>   technically isn't a rocket
> - no recovery charge required so should be deactivated.
> - designed to tumble after burnout
> - **New Zealand Rocketry Association safety code**
> - minimum dimensions of launch clear zone respective to motor (C
>   class)

***TODO***

- talk about simulations - are we using openrocket?
- Written assuming D motor

The rocket has a weight of **TODO** and a length of **TODO**.

According to the CAA Regulation 101.3 a rocket is defined as "a
pilotless vehicle propelled by a system that contains every ingredient
needed to form its own jet other than a rocket propelled by a model
rocket motor of size A-D which achieves no more than 20 Newton-seconds
of total impulse". As our rocket has a class D motor, and is achieves
**TODO: EXACT** under 20 Newton-seconds of thrust it is not classified
as a rocket by the CAA. Despite this, the team still aims to fully
comply with and follow their guidelines as if it were to be considered a
rocket.

The team also aims to fully comply with the NZ Model Rocketry Safety
Code. This means that the nose, body and fins of the rocket does not
contain any metal parts. It is built around a **TODO** motor from
**TODO** manufacturer, which contains **TODO** substances. This motor
will not be modified in any way from its manufactured state, nor will it
be used in anyway not recommended by the manufacturer.

The rocket has **TODO: EXACT** a recovery system, which ensures that the
rocket can return safely and undamaged from a flight.

The launch system for this rocket is electrical and uses electrical
motor ignitors. The launch system also has a safety interlock which
works in series with the launch switch.

Finally, the launch exclusion zone for a class D motor is 150 m in
diameter. This means that 75 m in all directions of the rocket must be
cleared before launch of the rocket.

## Section 2 - Launch Details

- see launch documents

### 2.1 - Travel Plan

> - heat required for ignition (288°)
> - rocket must be kept away from any source of heat > 50°
> - at all times multiple persons of contact present
> - mitigate getting lost or injured
> - mobile phones for communication
> - rocket classified as Class 1 Dangerous Goods according to **Land
>   Transport Rule: Dangerous Goods 2005**
>
> > - designated member of staff contacted upon return to confirm safety
> >   of participants
> > - if designated member receives no contact within an hour after
> >   expected arrival they should take emrgency.
> > - this action is laid out in launch documents

\[DRAFT]

To launch the rocket, the motor requires a temperature of 288 °C. To
mitigate any risks of accidental ignition; which may cause serious
damage or injury, the rocket must be kept away from any source of heat
greater than 50 °C. At all times during transportation, there must be
multiple persons of contact present. This can aid in any unforeseen
circumstances such as getting lost, injured or concerns about the
rocket. To ensure this communication is available, it is mandatory the
group must have at least one mobile device with enough credit for
texting / calls.

In accordance with the New Zealand Land Transport Rule:
[Dangerous Goods 2005](https://www.nzta.govt.nz/resources/rules/dangerous-goods-2005/),
the motor is classified as Class 1 under division
[§1.4](https://www.nzta.govt.nz/resources/rules/dangerous-goods-2005/#1).
To fulfill the requirements set out under the act, a designated member
of staff must be contacted upon return to confirm safety of
participants. In the circumstance that the designated member of staff
receives contact from the party within an hour after expected arrival.
They should immediately try to communicate with the party. If no contact
can be made, the designated member should take emergency action.
Alternative points of contact and actions to be undertaken will be laid
out within the launch documents.
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

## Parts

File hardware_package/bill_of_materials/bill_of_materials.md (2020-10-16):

# Bill of Materials

| COMPONENT | COST | NAME/DESCRIPTION/LINK | REASONS FOR CHOICE |
|:---|:---|:---|:---|
| Micro-Controller | $24.95 USD | Adafruit Feather STM32F405 (168MHz) [BUY](https://www.adafruit.com/product/4382), [Github](https://github.com/adafruit/Adafruit-Feather-STM32F405-Express-PCB), [Documentation](https://www.digikey.co.nz/en/videos/a/adafruit/programming-the-adafruit-feather-stm32f405-express-with-stm32cubeide-maker-io) | Small, Light, Good Opensource Libraries & Good Documentation |
| IMU | $17.59 NZD | MPU-6050 [BUY](https://www.digikey.co.nz/products/en?keywords=1528-3886-ND), [Datasheet](https://invensense.tdk.com/wp-content/uploads/2015/02/MPU-6000-Datasheet1.pdf), [adafruit library](https://github.com/adafruit/Adafruit_MPU6050) | Good Libraries, quaternions, Better Documentation, Very low price |
| GPS | $61.93 NZD | Adafruit Mini GPS PA1010D [BUY](https://www.digikey.co.nz/products/en?keywords=PA1010D), [Datasheet](https://cdn.taoglas.com/datasheets/GP.1575.25.4.A.02.pdf) | Cheap, Small and Meets requirments |
| Transceivers | $19.95 USD | Adafruit RFM96W LoRa Radio Transceiver Breakout - 433 MHz - RadioFruit [BUY](https://www.adafruit.com/product/3073), [Overview](https://learn.adafruit.com/adafruit-rfm69hcw-and-rfm96-rfm95-rfm98-lora-packet-padio-breakouts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), [Datasheet](https://cdn-learn.adafruit.com/downloads/pdf/adafruit-rfm69hcw-and-rfm96-rfm95-rfm98-lora-packet-padio-breakouts.pdf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) | SPI, Pins for extra antenna |
| Gimbal Servos | $6.97 NZD each | SERVOMOTOR RC 6V MICR METAL GEAR [BUY](https://www.digikey.com/product-detail/en/dfrobot/SER0011/1738-1232-ND/7087129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) | 15grams Small, Cheap, Has dimension specifications |
| Battery | $16 NZD | Giant Power 2s 7.4v 450mah 50c - E-Flite 130X [Buy](https://www.mrpositive.co.nz/giant-power-2s-7-4v-450mah-50c-e-flite-130x/) | -Available in NZ, - Sufficient Charge, Voltage and Current discharge specifications, - Cheap, -Light for a battery |
| Power supply | $3.62 USD | See power_supply.md | See power_supply.md |

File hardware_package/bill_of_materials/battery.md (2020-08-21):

# Battery

## Battery specifications

The largest rail is 5V so a higher battery voltage to handle any
overheads of the protection circuits etc.. must be accounted for.
Current draw must be greater than 700mA, and battery size must be enough
to supply the flight time.

## Recommendation

<https://hobbyking.com/en_us/zippy-compact-500mah-2s-35c-lipo-pack.html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>

This battery has a discharge of 35C (continuous) and capacity of 500mAh
at 7.4V (8.4-6.4V), giving plenty of run time and an plenty of discharge
rate. As of writing this the battery is in stock in Australia.

- Price: $12
- Weight: 35g
- Voltage Fully Charged: 8.4V
- Voltage just before cut off: 6.4V
- Capacity: 500mAh (3.7Wh)
- Max discharge rate: 45C ~ 22.5A
- continuous discharge rate: 35C ~17.5A

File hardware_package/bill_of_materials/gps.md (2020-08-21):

# Possible GPS modules

GPS modules for providing location of avionics package in the event, the
location of the package is unknown post flight.

## Top Pick

The M20048-1 is the best option. It is the most expensive out of the
options provided, however, it meets the accuracy requirements, connects
via UART and has low power consumption. Also contained within a small
package and has a detailed datasheet. As an alternative the J-F2-B3E8-Dr
could be used if the budget is tight. The STA8090WG & GP.1575.25.4.A.02,
are even cheaper options. The STA8090WG is mounted to the surface of the
PCB and GP.1575.25.4.A.02 is connected via pins and adhesive.

### Option 1

#### M20048-1

- "RADIONOVA® RF Receiver GPS 1.575GHz -165dBm On-Board, Trace Module"
- Link to store {Digi-Key):
  <https://www.digikey.co.nz/product-detail/en/antenova/M20048-1/627-1099-1-ND/7931498>
- Datasheet:
  <http://antenova.com/wp-content/uploads/2017/10/M20048-1-PS-1.0.pdfhttp://antenova.com/wp-content/uploads/2017/10/M20048-1-PS-1.0.pdf>
- Ports: UART
- Price NZD: $26.36
- Positional Accuracy (Horiz): <2.5m
- Cold start time: <35s

### Option 2

#### J-F2-B3E8-DR

- "Jupiter RF Receiver GPS 1.575GHz -163dBm On-Board, Trace Module"
- Link to store (Digi-Key):
  <https://www.digikey.co.nz/product-detail/en/telit/J-F2-B3E8-DR/943-1024-2-ND/4959429>
- Datasheet:
  <https://www.telit.com/wp-content/uploads/2012/01/Telit_Jupiter_JF2_Datasheet.pdf>
- Price NZD: $18.42
- Ports: UART, 1PPS, I^2C and SPI
- Positional accuracy to <2.5m
- Cold stat time: <35s

### Option 3

#### STA8090WG

- "RF Receiver BeiDou, Galileo, GLONASS, GNSS, GPS -162dBm 12Mbps PCB,
  Surface Mount 77-WLCSP (3.86x3.84)""
- Link (Digi-Key):
  <https://www.digikey.co.nz/product-detail/en/stmicroelectronics/STA8090WG/497-19034-2-ND/9990053>
- Datasheet: <https://www.st.com/resource/en/datasheet/sta8090wg.pdf>
- Price NZD: $7.10852
- Ports: I²C, SPI, UART, USB

### Option 4

#### GP.1575.25.4.A.02

- "1.575GHz GPS Ceramic Patch RF Antenna 1.570GHz ~ 1.580GHz 1.55dBic
  Pin Adhesive"
- Link (Digi-key):
  <https://www.digikey.co.nz/product-detail/en/taoglas-limited/GP-1575-25-4-A-02/931-1015-ND/2332642>
- Datasheet:
  <https://www.taoglas.com/images/product_images/original_images/GP.1575.25.4.A.02%20GPS%20Patch%20Antenna%201575MHz%20190410.pdf>
- Price NZD: $7.50

### Best option

#### Adafruit Mini GPS PA1010D Module

- [Adafruit](https://learn.adafruit.com/adafruit-mini-gps-pa1010d-module)
- [Digikey](https://www.digikey.co.nz/products/en?keywords=PA1010D)
- Library

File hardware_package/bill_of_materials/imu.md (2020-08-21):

# IMU Possible Options

## ICM-20602

- Link to product store:
  [digikey](https://www.digikey.co.nz/product-detail/en/tdk-invensense/ICM-20602/1428-1060-1-ND/5872875)
- [Data sheet](https://invensense.tdk.com/wp-content/uploads/2016/10/DS-000176-ICM-20602-v1.0.pdf?ref_disty=digikey)
- [Possible library](https://github.com/ArduPilot/ardupilot/blob/master/libraries/AP_InertialSensor/AP_InertialSensor_Invensense.cpp)
- Price $6.55

## BNO055

- Link to product store:
  [Mouser](https://nz.mouser.com/ProductDetail/Bosch-Sensortec/BNO055?qs=QhAb4EtQfbV8Z2YmISucWw%3D%3D)
- [Data sheet](https://nz.mouser.com/datasheet/2/783/BST-BNO055-DS000-1509603.pdf)
- [Adafruit Arduino library](https://learn.adafruit.com/adafruit-bno055-absolute-orientation-sensor/arduino-code)
- Price $17.59\

This library has a lot of built in functionality and is well documented,
which should allow for easy use. It also has the ability to return both
Euler angles, along with quaternions. This should allow for easier, and
less CPU intensive processing of the rocket orientation. There is also a
large selection of available breakout boards for this IMU, which would
allow for prototyping before a PCB is designed and ordered.

## MPU-6050

- Link to product store:
  [Mouser](https://nz.mouser.com/ProductDetail/TDK-InvenSense/MPU-6050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)
- [Data sheet](https://invensense.tdk.com/wp-content/uploads/2015/02/MPU-6000-Datasheet1.pdf)
- [Library](https://github.com/jrowberg/i2cdevlib/tree/master/Arduino/MPU6050)
- [adafruit library](https://github.com/adafruit/Adafruit_MPU6050)
- [Arduino description page](https://playground.arduino.cc/Main/MPU-6050/)
- Price $12.73

This library is really extensive and might be able to handle the control
systems for us as it has built in PID and KI & KP calculators. It Is
also a very complex library however which may take a very long time to
get a handle on... This should be made easier by the available examples
in the library. There is also a large selection of available breakout
boards for this IMU, which would allow for prototyping before a PCB is
designed and ordered.

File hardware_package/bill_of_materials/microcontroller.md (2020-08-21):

# Micro-Controller options

## Adafruit Feather STM32F405

- Link to buy from [Adafruit](https://www.adafruit.com/product/4382)
- Schematic
  [Github](https://github.com/adafruit/Adafruit-Feather-STM32F405-Express-PCB)
- Programming help
  [Adafruit](https://www.digikey.co.nz/en/videos/a/adafruit/programming-the-adafruit-feather-stm32f405-express-with-stm32cubeide-maker-io)

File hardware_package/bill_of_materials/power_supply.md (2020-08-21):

# Power Supply

Note: This may change regularly as power requirements change as
different components are selected or new considerations are realized.

To properly understand the costs and specifications of the power supply
and battery, Prototypes of the power supplies for each voltage rail must
be designed. This will be done based on the following list.

| COMPONENT | Current Draw Max | Voltage Range | Max Power | Notes |
|:---|:---|:---|:---|:---|
| Micro-Controller | 80mA + (anything its supplies) | 4.2-3.7V or (5V?) | 0.336W | Adafruit STM32F405 Feather Express can be powered by USB-will also take battery into the JST jack, This can also charge the Battery when powered by USB @ 100mA, (Maybe could supply Via USB at 5V to reduce number of rails?) |
| IMU | 13.7mA | 2.4-3.6V | 0.04932W  | The highest values of the two IMUs were selected |
| GPS (Estimates) | 25mA | 3-4V | 0.1W | |
| Transceivers | 20-33mA | 3-5V | 0.1W | Has onboard regulation to 3.3V, so ideally this would connect to a 3.3V rail |
| Gimbal Servos (Estimates) | 5-250mA | 4.8-6V | 1.5W | Servos Draw a small amount of idle current, when activated, this can jump up greatly |
| - | 660mA | Rails: 5V, 3.3V | ~3.6W | |

## Rail specifications

| Rail | Components | Current Draw Max | Max Power OUT | Notes | | |
|:---|:---|:---|:---|:---|:---|:---|
| 3.3V | IMU, GPS, | | | | | |
| Transceiver | ~72mA | 0.25W | This rail could be provided by the | | | |
| Microcontroller | | 5V | Servos | 500mA | 3W | |
| 4V | Microcontroller++ | ~152.5mA | ~0.6W | | | |

## Battery specifications

The largest rail is 5V so a higher battery voltage to handle any
overheads of the protection circuits etc.. must be accounted for.
Current draw must be greater than 700mA, and battery size must be enough
to supply the flight time.

Selected Battery has the following relevant specifications:

- Voltage Fully Charged: 8.4V
- Voltage just before cut off: 6.4V
- Capacity: 500mAh (3.7Wh)
- Max discharge rate: 45C ~ 22.5A
- continuous discharge rate: 35C ~17.5A

So the power supplies must take a 6.4-8.4V input and supply their
respective Voltages. The desired optimizations for these DC-DC supplies
are Firstly Minimal footprint, and then efficiency. As a low efficiency
will mean more power must be supplied by the battery and a hotter
operating temperature.

## Power Supply BOM

Designs, Performance diagrams and BOMs for the power supplies are in
the Prototypes folder of the hardware section of the directory

| Supply Output Voltage | Footprint | Cost | Efficiency | Power Dissipated | MAX Rail Power Draw |
|:---|:---|:---|:---|:---|:---|
| 4V | 77mm<sup>2</sup>  | $1.50 USD | 95.5% | ~0.035W @ 150mA  | 0.635W |
| 5V | 143mm<sup>2</sup> | $2.15 USD | 97.3% | ~0.09W @ 600mA | 3.69W |
| **Totals** | 220mm<sup>2</sup> | $3.62 USD | - | 0.125W | **3.745W** |

Note: the BOMs for these may not contain Components available in NZ,
When the designs are finalized parts with the same characteristics will
be chosen that can be delivered to NZ.

The overall power supply is not complete, need to design the Ignition
system and the protection circuits before this list can be complete.

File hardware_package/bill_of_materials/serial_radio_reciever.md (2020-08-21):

# Radio Receiver

A component/s to receive data from the rocket and convert data to a
format that can be handled by the "Ground control" Team. The
requirements for this are that it interfaces via USB, and can receive
data from the 433MHz band. (LoRa modulation is suggested or LoRa is
Required?)

| Product | Unit Cost | Desc. | Advantages | Disadvantages | Link |
|:---|:---|:---|:---|:---|:---|
| RC1140-RC232 () | $25.49550 NZD  | General ISM < 1GHz RC232 Transceiver Module 433MHz ~ 434MHz Antenna Not Included, Castellation Surface Mount, UART Serial interface (GFSK protocol) | -Low power requirements -Relatively cheap -comprehensive data sheet -Transceiver | -Surface Mounting IC, needs construction. | <https://www.digikey.co.nz/product-detail/en/radiocrafts-as/RC1140-RC232/1783-1031-1-ND/7100633> |
| RC1140-MBUS3-USB | $187.46150 NZD | RF Transceiver, WIRELESS M-BUS 433 MHZ USB, (802.15.4 Zigbee™ protocol) | - Already has usb interface and protocol, -Transceiver, -Powered by USB port | -Cost | <https://www.digikey.co.nz/product-detail/en/radiocrafts-as/RC1140-MBUS3-USB/1783-RC1140-MBUS3-USB-ND/10709711> |
| MAX1473EUI+T | $12.32800 NZD  | ASK data modulated in the 300MHz to 450MHz range | -Low Power, -Very cheap. | -just an IC | <https://www.digikey.co.nz/product-detail/en/maxim-integrated/MAX1473EUI-T/MAX1473EUI-TCT-ND/3679891> |
| RXM-433-LR | $34.84500 NZD  | Data Interface Serial, RF RECEIVER protocol(ASK/OOK) 433MHZ | 2.1V ~ 3.6V | IC | |
| SX1276MB1LAS | $129.24850 NZD | General ISM < 1GHz Transceiver Module 137MHz ~ 1.02GHz Antenna Not Included, SMA Through Hole (SPI serial interface) | Modulation  FSK, GFSK, GMSK, MSK, OOK, | Antenna Not Included, | <https://www.digikey.co.nz/product-detail/en/semtech-corporation/SX1276MB1LAS/SX1276MB1LAS-ND/5015647> |
| SX1261IMLTRT | $14.84650 NZD  | IC RF TxRx Only General ISM < 1GHz LoRaWAN 150MHz ~ 960MHz 24-VFQFN Exposed Pad (SPI Serial interfaces) | | | |
| 109990165 Seed Studio | $12.75 | General ISM < 1GHz LoRa™ Transceiver Module 433MHz Surface Mount SPI | Available libraries and breakout board for easy testing | Uses the BGA package type, however this component is non-critical to the control of the rocket, therefore it is less of an issue | <https://www.seeedstudio.com/Grove-LoRa-Radio-868MHz.html> <https://www.digikey.co.nz/product-detail/en/seeed-technology-co-ltd/109990165/1597-1491-ND/7033235> (433MHz <https://www.seeedstudio.com/Grove-LoRa-Radio-433MHz-p-2777.html)> |
| Adafruit RFM69HCW and RFM9X LoRa | $19.95 | General ISM < 1GHz LoRa™ Transceiver Module 433MHz Surface Mount SPI | Available libraries and breakout board for easy testing | Uses the BGA package type, however this component is non-critical to the control of the rocket, therefore it is less of an issue | <https://www.adafruit.com/product/3073> <https://learn.adafruit.com/adafruit-rfm69hcw-and-rfm96-rfm95-rfm98-lora-packet-padio-breakouts/rfm9x-test> <http://www.airspayce.com/mikem/arduino/RadioHead/> |

## Notes

Radiocrafts has the best options that have been found. Large
range of products regarding Comms. all seem good quality. only a few
433MHz products, all seem to be Transceivers which may be harder to set
up, if the IC way was the choice. The USB RF-Transceiver they make is
comparatively cheap (Compared to FUNdongle).

Most of the options will require antenna and a DC-DC power supply, along
with a communication channel to a USB port (must construct a fair bit of
shit cost might increase substantially).

There are several LoRa options that will need ^, the full usb units are
out of our budget.

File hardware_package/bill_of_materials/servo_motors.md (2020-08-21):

# Servos

Required for the Gimbal. Desired specifications are, Low profile, decent
torque, ideally very light, cheap and low power draw. Voltage range
(within 3-7V). (want to update servos around 40Hz should complete 0.5
rpm in 1/40seconds so RPM should be around 20+)

| Product | Strength | RPM | Voltage Range | Peak current Draw | Weight | Dimensions | Price | Link |
|:---|:---|:---|:---|:---|:---|:---|:---|:---|
| ROB-16413 | - | 90 RPM (4.5V) | 3 ~ 9VDC | - | ? | 80x22.4x25.8mm | $12.30500 | <https://www.digikey.co.nz/product-detail/en/sparkfun-electronics/ROB-16413/1568-ROB-16413-ND/12178435> |
| 2442 | 147.4(mNm) | 130() | 4.8-6V | 100 mA | 9.07 g | 32mm x 30mm x 12mm | $15.51350 | <https://www.digikey.co.nz/product-detail/en/adafruit-industries-llc/2442/1528-1501-ND/5774227> |
| SER0039 | 1.8kg*cm torque | 130 | 4.8~6V | - | 12 grams | 22.3 x 11.8 x 26.3 mm | $12.32800 | <https://www.digikey.co.nz/product-detail/en/dfrobot/SER0039/1738-1255-ND/7087152> |

## Notes

### Brushed

- Low overall construction costs;
- Simple and inexpensive controller; <----------
- Controller not needed for fixed speed;
- Ideal for extreme operating environments. <----------

### Brushless

- Less overall maintenance due to lack of brushes;
- Operates effectively at all speeds with rated load;
- High efficiency and high output power to size ratio; <----------
- Reduced size with far superior thermal characteristics; <----------
- Higher speed range and lower electric noise generation. <----------

ref:
<https://www.motioncontrolonline.org/blog-article.cfm/Brushed-DC-Motors-Vs-Brushless-DC-Motors/24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,as%20a%20two%2Dpole%20electromagnet.&text=A%20brushless%20motor%2C%20by%20contrast,magnet%20as%20its%20external%20rotor.>

### Stepper vs Servo

"The basic difference between a traditional stepper and servo-based
system is the type of motor and how it is controlled. Steppers typically
use 50 to 100 pole brushless motors while typical servo motors have only
4 to 12 poles. A pole is an area of a motor where a North or South
magnetic pole is generated either by a permanent magnet or by passing
current through the coils of a winding.

Steppers don't require encoders since they can accurately move between
their many poles whereas servos, with few poles, require an encoder to
keep track of their position. Steppers simply move incrementally using
pulses \[open loop] while servo's read the difference between the motors
encoder and the commanded position \[closed loop], and adjust the current
required to move."

#### ADV/DISADV

- "One rotation of a stepper motor requires many more current exchanges
  through the windings than a servo motor."
- "he stepper motor's design results in torque degradation at higher
  speeds when compared to a servo"
- "Conversely, a high pole count has a beneficial effect at lower speeds
  giving the stepper motor a torque advantage over the same size servo
  motor."

"Servo control systems are best suited to **high speed**, **high
torque** applications that involve **dynamic load changes**. Stepper
control systems are **less expensive** and are optimal for applications
that require **low-to-medium acceleration**, **high holding torque**,
and the flexibility of open or closed loop operation."

ref:
<https://www.amci.com/industrial-automation-resources/plc-automation-tutorials/stepper-vs-servo/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,when%20compared%20to%20a%20servo.>

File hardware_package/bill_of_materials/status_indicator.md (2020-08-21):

# Status Indicator(s) Components

## Magnetic buzzer transducer for Arm State

- [DigiKey](https://www.digikey.co.nz/product-detail/en/cui-devices/CEM-1203-42/102-1153-ND/412412),
- [Data Sheet](https://www.cuidevices.com/product/resource/cem-1203-42-.pdf).

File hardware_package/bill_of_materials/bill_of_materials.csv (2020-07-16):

Supplier | Supplier Part Number | Manufacturer Part Number | Qty | Description | Price Indivdual | Total
Digi-key | 1738-1232-ND | SER0011 | 3 | DC Motor Servomotor, RC (Hobby) 6VDC | 14.4095 | 43.2285
Digi-key | 1597-1491-ND | 109990165 | 2 | General ISM < 1GHz LoRa™ Transceiver Module 433MHz Surface Mount | 14.6625 | 29.325
Digi-key | 1528-3886-ND | 3886 | 1 | MPU-6050 - Accelerometer, Magnetometer Sensor Evaluation Board | 14.375 | 14.375
Digi-key | 1528-4382-ND | 4382 | 1 | STM32F405 Feather STM32F405 Express STM32F4 ARM® Cortex®-M4 MCU 32-Bit Embedded Evaluation Board | 51.6005 | 51.6005
Digi-key | 1528-1034-ND | 1893 | 1 | MPL3115A2 - Pressure, Temperature Sensor Evaluation Board | $20.57 | 20.5735
 |  |  |  |  |  | 159.1025

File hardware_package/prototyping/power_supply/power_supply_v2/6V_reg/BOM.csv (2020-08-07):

Part | Manufacturer | Part Number | Quantity | Price ($) | Footprint (mm²) | Description
Coutx | TDK | C1608X5R1E106M080AC | 1 | 0.2 | 4.68 | Cap: 10 µF Total Derated Cap: 2.7 µF VDC: 25 V ESR: 4.64 mΩ Package: 0603
Rfbt | Yageo | RC0603FR-07649KL | 1 | 0.01 | 4.68 | Resistance: 649 kΩ Tolerance: 1.0% Power: 100 mW
Cout | TDK | C3216X5R1E476M160AC | 1 | 0.39 | 10.92 | Cap: 47 µF Total Derated Cap: 14 µF VDC: 25 V ESR: 2.08 mΩ Package: 1206
L1 | Bourns | SDR0805-1R5ML | 1 | 0.27 | 96.04 | L: 1.5 µH DCR: 20 mΩ IDC: 6 A
Cin | MuRata | GRM32ER61C476KE15L | 1 | 0.38 | 14.7 | Cap: 47 µF Total Derated Cap: 20 µF VDC: 16 V ESR: 3.04 mΩ Package: 1210
U1 | Texas Instruments | TPS63070RNMR | 1 | 0.88 | 14
Caux | MuRata | GRM155R71C104KA88D | 1 | 0.01 | 3 | Cap: 100 nF Total Derated Cap: 100 nF VDC: 16 V ESR: 1 mΩ Package: 0402
Rfbb | Vishay-Dale | CRCW0603100KFKEA | 1 | 0.01 | 4.68 | Resistance: 100 kΩ Tolerance: 1.0% Power: 100 mW
Renable | Yageo | RC0201FR-0710KL | 1 | 0.01 | 2.08 | Resistance: 10 kΩ Tolerance: 1.0% Power: 50 mW
Rpgood | Vishay-Dale | CRCW0603100KFKEA | 1 | 0.01 | 4.68 | Resistance: 100 kΩ Tolerance: 1.0% Power: 100 mW

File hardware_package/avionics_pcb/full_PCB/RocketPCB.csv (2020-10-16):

Refs | Field10 | Field4 | Field5 | Field6 | Field7 | Field8 | Field9 | datasheet | footprint | value
C1 |  |  |  |  |  |  |  | ~ |  | 22pF
C10 |  |  |  |  |  |  |  | ~ |  | 10uF
C11 |  |  |  |  |  |  |  | ~ |  | 22uF
C12 |  |  |  |  |  |  |  | ~ |  | 10uF
C13 |  |  |  |  |  |  |  | ~ |  | 0.1u
C14 |  |  |  |  |  |  |  | ~ |  | 2.2u
C15 |  |  |  |  |  |  |  | ~ |  | 10uF
C16 |  |  |  |  |  |  |  | ~ |  | 10uF
C17 |  |  |  |  |  |  |  | ~ |  | 1uF
C18 |  |  |  |  |  |  |  | ~ |  | 100nF
C19 |  |  |  |  |  |  |  | ~ |  | 1uF
C2 |  |  |  |  |  |  |  | ~ |  | 22pF
C20 |  |  |  |  |  |  |  | ~ |  | 10uF
C21 |  |  |  |  |  |  |  | ~ |  | 1uF
C22 |  |  |  |  |  |  |  | ~ |  | 10uF
C23 |  |  |  |  |  |  |  | ~ |  | 1uF
C24 |  |  |  |  |  |  |  | ~ |  | 100nF
C25 |  |  |  |  |  |  |  | ~ |  | 1uF
C26 |  |  |  |  |  |  |  | ~ |  | 1uF
C27 |  |  |  |  |  |  |  | ~ |  | 1uF
C3 |  |  |  |  |  |  |  | ~ |  | 22pF
C4 |  |  |  |  |  |  |  | ~ |  | 10uF
C5 |  |  |  |  |  |  |  | ~ |  | 0.1uF
C6 |  |  |  |  |  |  |  | ~ |  | 10uF
C7 |  |  |  |  |  |  |  | ~ |  | 22pF
C8 |  |  |  |  |  |  |  | ~ |  | 0.1uF
C9 |  |  |  |  |  |  |  | ~ |  | 10uF
D1 |  |  |  |  |  |  |  | ~ |  | LED
D2 |  |  |  |  |  |  |  | ~ |  | D
D3 |  |  |  |  |  |  |  | http://www.mccsemi.com/up_pdf/MBR0520~MBR0580(SOD123).pdf | Diode_SMD:D_SOD-123 | MBR0540
FB1 |  |  |  |  |  |  |  | ~ |  | Ferrite_Bead
J1 |  |  |  |  |  |  |  | https://www.usb.org/sites/default/files/documents/usb_type-c.zip |  | USB_C_Receptacle
J2 |  |  |  |  |  |  |  | http://katalog.we-online.de/em/datasheet/693072010801.pdf |  | Micro_SD_Card
J3 |  |  |  |  |  |  |  | ~ | Connector_JST:JST_XH_B3B-XH-A_1x03_P2.50mm_Vertical | Conn_01x03_Female
L1 |  |  |  |  |  |  |  | ~ |  | 2.2uH
Q1 |  |  |  |  |  |  |  | https://www.diodes.com/assets/Datasheets/DMG2301L.pdf | Package_TO_SOT_SMD:SOT-23 | DMG2301L
R1 |  |  |  |  |  |  |  | ~ |  | 10k
R10 |  |  |  |  |  |  |  | ~ |  | 100k
R11 |  |  |  |  |  |  |  | ~ |  | 649k
R12 |  |  |  |  |  |  |  | ~ |  | 180k
R13 |  |  |  |  |  |  |  | ~ |  | 100k
R14 |  |  |  |  |  |  |  | ~ |  | 10k
R15 |  |  |  |  |  |  |  | ~ |  | 100k
R16 |  |  |  |  |  |  |  | ~ |  | 100k
R17 |  |  |  |  |  |  |  | ~ |  | 10k
R18 |  |  |  |  |  |  |  | ~ |  | 10k
R19 |  |  |  |  |  |  |  | ~ |  | 10k
R2 |  |  |  |  |  |  |  | ~ |  | 5.1k
R3 |  |  |  |  |  |  |  | ~ |  | 5.1k
R4 |  |  |  |  |  |  |  | ~ |  | 100k
R5 |  |  |  |  |  |  |  | ~ |  | 2.2k
R6 |  |  |  |  |  |  |  | ~ |  | 100k
R7 |  |  |  |  |  |  |  | ~ |  | 100k
R8 |  |  |  |  |  |  |  | ~ |  | 100k
R9 |  |  |  |  |  |  |  | ~ |  | 10k
SW1 |  |  |  |  |  |  |  | ~ |  | SW_Push
SW2 |  |  |  |  |  |  |  | ~ |  | SW_Push
U1 |  |  |  |  |  |  |  | http://www.st.com/st-web-ui/static/active/en/resource/technical/document/datasheet/DM00037051.pdf | Package_QFP:LQFP-64_10x10mm_P0.5mm | STM32F405RGTx
U2 |  |  |  |  |  |  |  | http://www.ti.com/lit/ds/symlink/tps62160.pdf | Package_SON:WSON-8-1EP_2x2mm_P0.5mm_EP0.9x1.6mm_ThermalVias | TPS62160DSG
U3 |  |  |  |  |  |  |  | http://www.hoperf.com/upload/rf/RFM69HCW-V1.1.pdf |  | RFM69HCW
U4 | MPU-6050 | TDK | Good | 3.4 | QFN-24 InvenSense | IPC-7351B | 5.45 USD |  | QFN50P400X400X95-24N | MPU-6050
U5 |  | F | IPC-7351B |  |  |  |  | Winbond | SOIC127P790X216-8N | W25Q16BVSSIG
U6 |  |  |  |  |  |  |  | https://www.diodes.com/assets/Datasheets/AP2112.pdf | Package_TO_SOT_SMD:SOT-23-5 | AP2112K-3.3
U7 |  |  |  |  |  |  |  | https://www.nxp.com/docs/en/data-sheet/MPL3115A2.pdf | Package_LGA:NXP_LGA-8_3x5mm_P1.25mm_H1.1mm | MPL3115A2
X1 |  |  |  |  |  |  |  |  |  | GPS_PA1010D
Y1 |  |  |  |  |  |  |  | ~ |  | 12MHz
Y2 |  |  |  |  |  |  |  | ~ |  | 32.768

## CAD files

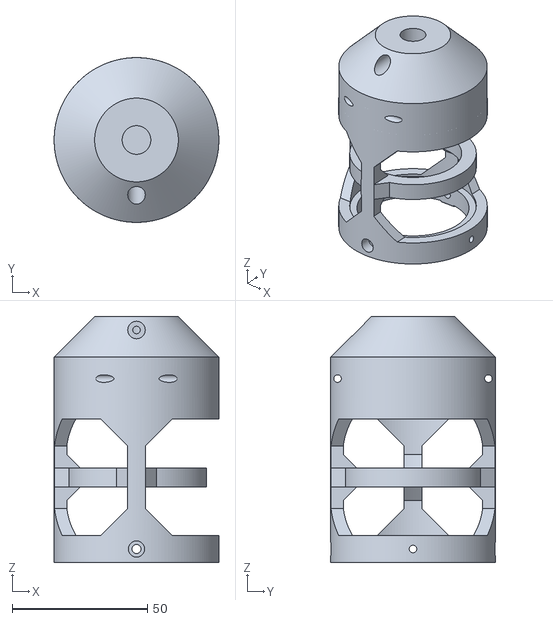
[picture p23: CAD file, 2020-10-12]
hardware_package/prototyping/rocket_body/gimbal/prototype_4/print_files/part_3.stl
61.0 x 61.0 x 91.1

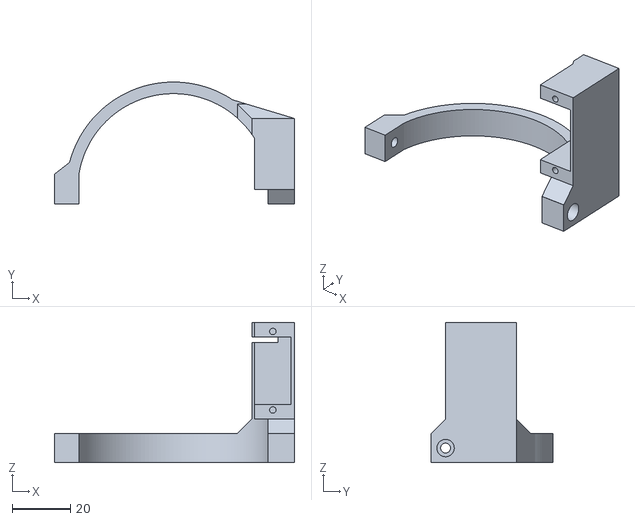
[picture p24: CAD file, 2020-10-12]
hardware_package/prototyping/rocket_body/gimbal/prototype_4/print_files/part_5.stl
82.7 x 42.0 x 48.3

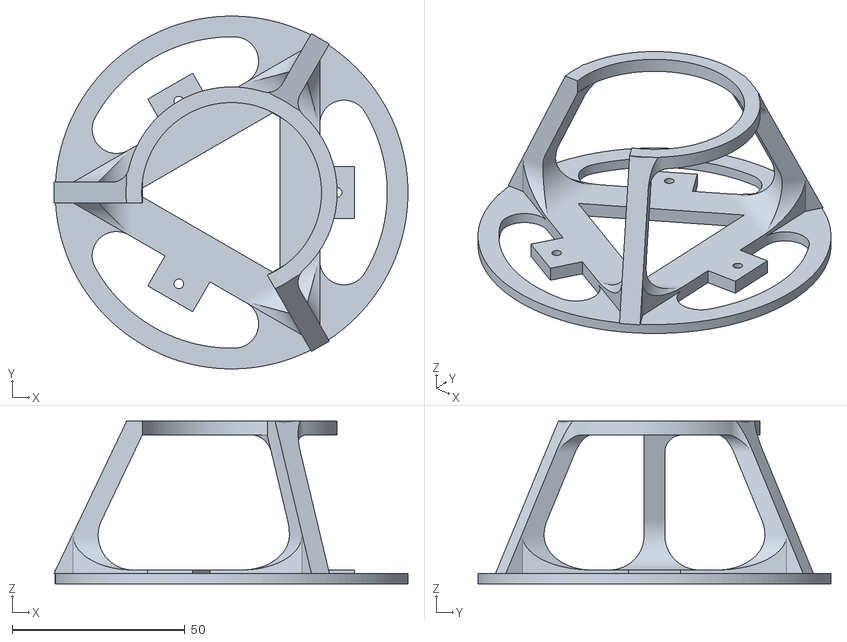
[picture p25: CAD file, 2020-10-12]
hardware_package/prototyping/rocket_body/gimbal/prototype_4/print_files/part_4.stl
102.3 x 102.0 x 47.0

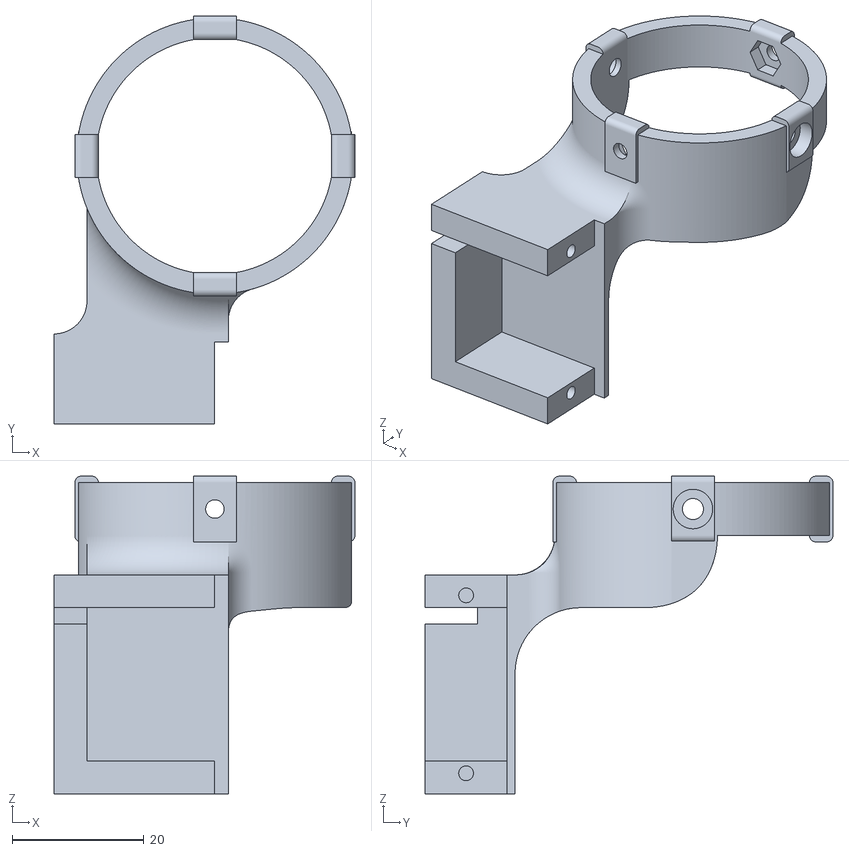
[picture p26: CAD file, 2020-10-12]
hardware_package/prototyping/rocket_body/gimbal/prototype_4/print_files/part_2.stl
45.7 x 62.0 x 48.3

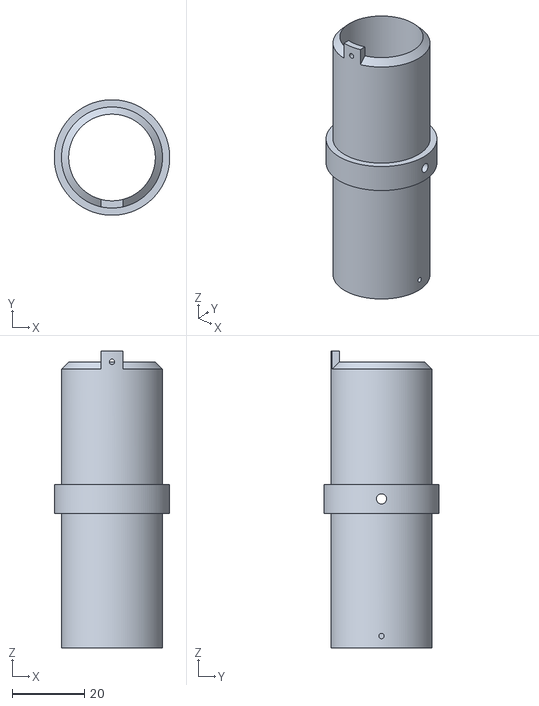
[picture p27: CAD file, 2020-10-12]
hardware_package/prototyping/rocket_body/gimbal/prototype_4/print_files/part_1_.stl
32.0 x 32.0 x 82.3

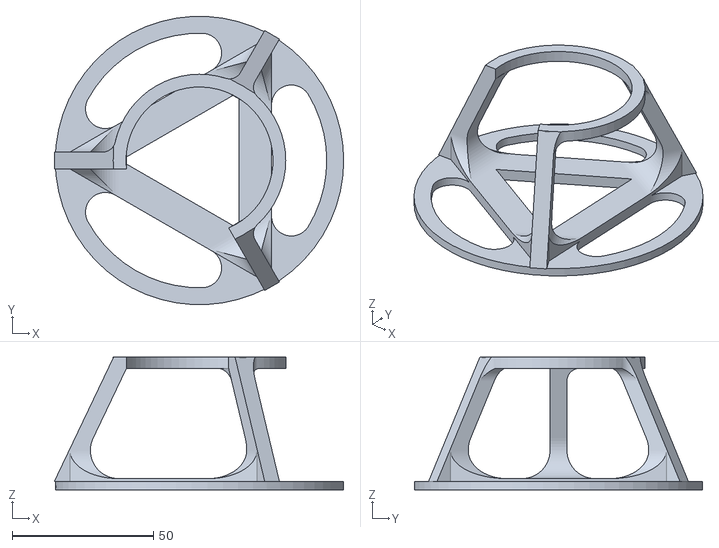
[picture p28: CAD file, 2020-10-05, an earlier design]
hardware_package/prototyping/rocket_body/gimbal/prototype_3/print_files/stand.stl
102.3 x 101.9 x 47.0

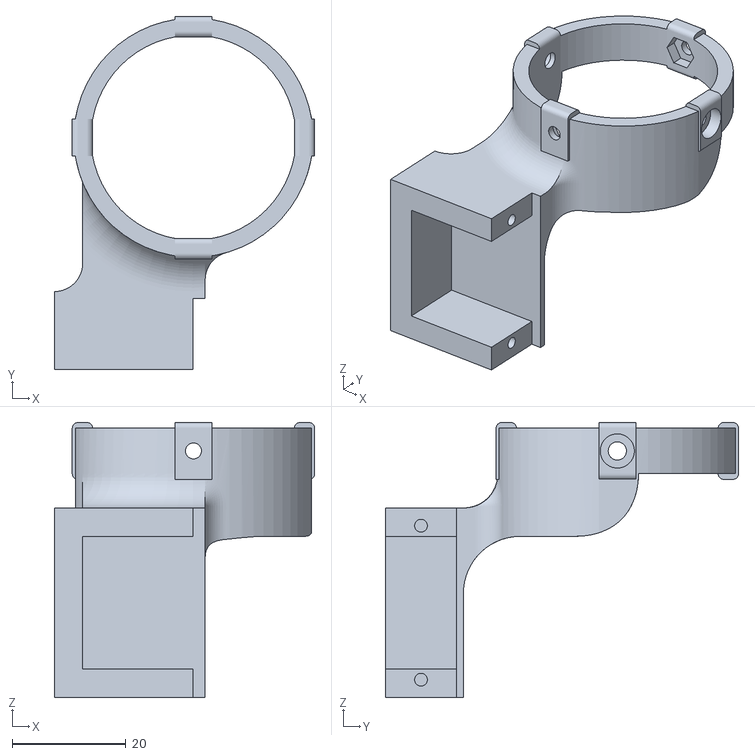
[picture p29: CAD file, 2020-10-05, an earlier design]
hardware_package/prototyping/rocket_body/gimbal/prototype_3/print_files/lower_mount.stl
45.7 x 62.0 x 48.3

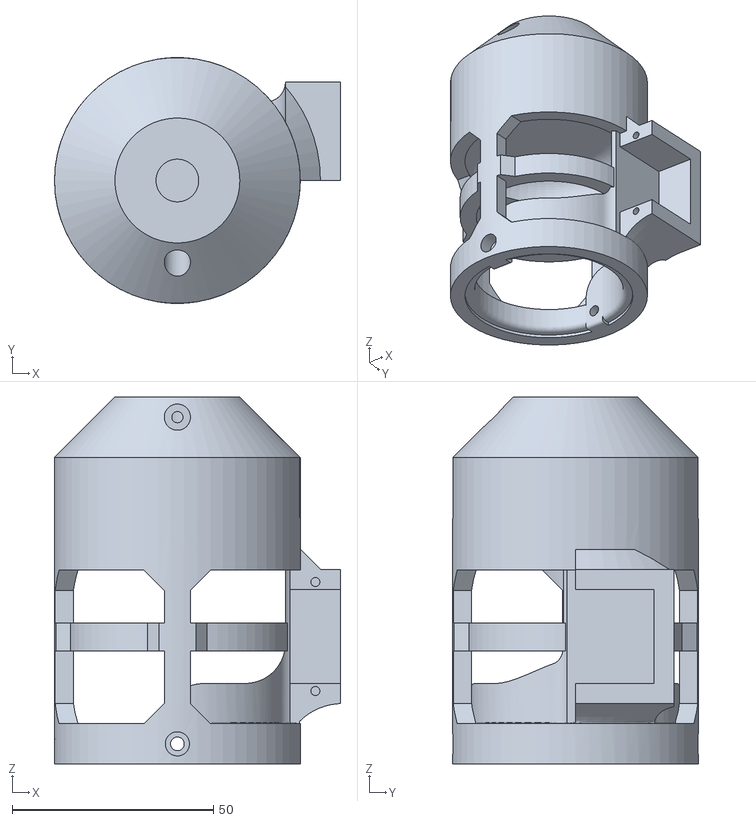
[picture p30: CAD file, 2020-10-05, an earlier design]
hardware_package/prototyping/rocket_body/gimbal/prototype_3/print_files/upper_mount.stl
71.0 x 61.0 x 91.1

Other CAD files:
hardware_package/prototyping/rocket_body/gimbal/prototype_3/print_files/engine_tube.stl
hardware_package/prototyping/rocket_body/combined_3d_model/assembly_model_files/Assembly 1.x_t
hardware_package/prototyping/rocket_body/gimbal/prototype_1/assembly/files/Assembly 1.x_t
hardware_package/prototyping/rocket_body/gimbal/prototype_1/cad_files/Bottom_Servo_Mount.x_t
hardware_package/prototyping/rocket_body/gimbal/prototype_1/cad_files/Tube.x_t
hardware_package/prototyping/rocket_body/gimbal/prototype_1/cad_files/Upper_Servo_Mount.x_t
hardware_package/prototyping/rocket_body/gimbal/prototype_2/assembly/files/assembly_1.x_t
hardware_package/prototyping/rocket_body/gimbal/prototype_2/cad_files/inner.x_t
hardware_package/prototyping/rocket_body/gimbal/prototype_2/cad_files/outer.x_t
hardware_package/prototyping/rocket_body/gimbal/prototype_2/cad_files/tube.x_t
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

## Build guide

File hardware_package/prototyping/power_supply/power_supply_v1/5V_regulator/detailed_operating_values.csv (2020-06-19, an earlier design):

Name | Value | Category | Description
Vout | 5 V | System Information | Operational Output Voltage
IC Tolerance | 10 mV | IC | IC Feedback Tolerance
Cin IRMS | 954.34 mA | Capacitor | Input capacitor RMS ripple current
Cin Pd | 2.05 mW | Capacitor | Input capacitor power dissipation
Cout IRMS | 266.1 mA | Capacitor | Output capacitor RMS ripple current
Cout Pd | 131.35 µW | Capacitor | Output capacitor power dissipation
Duty Cycle | 68.56% | System Information | Duty cycle
Efficiency | 97.3% | System Information | Steady state efficiency
Frequency | 523.91 kHz | System Information | Switching frequency
IC Tj | 44.26 °C | IC | IC junction temperature
ICThetaJA | 60 °C/W | IC | IC junction-to-ambient thermal resistance
L Ipp | 921.8 mA | Inductor | Peak-to-peak inductor ripple current
L Pd | 35.01 mW | Inductor | Inductor power dissipation
IC Pd | 237.59 mW | IC | IC power dissipation
Pout | 10 W | System Information | Total output power
Iin Avg | 1.39 A | IC | Average input current
IC Ipk | 2.46 A | IC | Peak switch current in IC
Mode | CCM | System Information | Conduction Mode
Vout p-p | 24.25 mV | System Information | Peak-to-peak output ripple voltage
Total Pd | 275.16 mW | Power | Total Power Dissipation
FootPrint | 143 mm² | System Information | Total Foot Print Area of BOM components
Vin | 7.4 V | System Information | Vin operating point
Iout | 2 A | System Information | Iout operating point
Cin Pd | 2.05 mW | Power | Input capacitor power dissipation
Cout Pd | 131.35 µW | Power | Output capacitor power dissipation
L Pd | 35.01 mW | Power | Inductor power dissipation
IC Pd | 237.59 mW | Power | IC power dissipation
Vout Actual | 4.96 V | System Information | Vout Actual calculated based on selected voltage divider resistors
Vout Tolerance | 3.04% | System Information | Vout Tolerance based on IC Tolerance (no load) and voltage divider resistors if applicable
Total BOM | $2.15 | System Information | Total BOM Cost
BOM Count | 10 | System Information | Total Design BOM count

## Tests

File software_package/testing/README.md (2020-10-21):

# Testing

As explained in the software_package
[README](./software_package/README.md) this directory is solely
dedicated to the testing of the hardware, and/or other aspects of the
software system. For the most part the focus on this package is about
gaining an understanding of the specific hardware components and the
libraries attached to them. This also serves as a 'playground' to
determine how to approach a given task from a technical/practical
perspective. This includes getting each of these working inside of the
PIO structure.

The key goal of this package can be viewed as creating code that works.
That which can than be iterated on and refined both here and in the
`development` package. Due to the experimental nature of this package
there is little structure to each package, with most testing packages
just containing a single `main.cpp`.

## Testing Projects

### Lora testing

This package is and was used for the initial setup of the base station,
which is critical for all communication with Mission Control. The
communication for base station was achieved via the LoRa radio module.
This package contains two further PIO project packages: `Lora STM32` for
the transmission of packets, and `Lora Base Station` for the reading of
packets,.

On of the key discoveries in this process was that the LoRa module
struggled to perform communication at a reasonable frequency. A lot of
this package contains the tuning and tweaking of the LoRa software to
best optimise this transmission rate.

### Generic Testing

This package is and was used for testing a wide range of the components
individually. This includes custom methods, eg. double_test(), for
testing the effectiveness and limitations of performing calculations on
the hardware.

The first iteration of our MPU and SD interaction can also be found
here. This includes logic for initializing components, reading
accelerometer and gyroscope values, adjusting filter bandwidth values,
and reading and writing from files.

### Quaternion Testing

The [`mpu_quat_testing`](./mpu_quat_testing) package is dedicated to
determining how the IMU can angle readings in quaternions. This project
involves some interaction with the i2cdev library for the handling of
quaternions. See
[this issue](https://gitlab.ecs.vuw.ac.nz/course-work/engr300/2020/group3/group-3/-/issues/175)
for more details.

### Servo Testing

The [`mpu_servo_testing`](./mpu_servo_testing) and
[`servo_testing`](./servo_testing) packages gives some insight on how
the software system can interface with the servos of the rocket in order
to get the gimbal to respond to angle readings given by the IMU. The
`mpu_servo_testing` package is explores how the quaternion readings can
be used by the servos, while the `servo_testing` package explores the
usage of methods provided by the adafruit libraries to make the servos
move.

### Testing Environment Experiment

The package
[`testing_environment_experiment`](./testing_environment_experiment) is
a PIO project that demonstrates the CI/CD pipeline capabilities of the
project with regards to unit testing and code coverage, and existing
issues with the current implementation of the CI/CD pipeline.

To demonstrate the CI/CD unit testing and code coverage, this project
contains source code that has no dependencies with adafruit libraries
(e.g the state machine of the software system). This highlights an issue
with the current implementation of the CI/CD of the project. As it
currently stands, the CI/CD pipeline is incapable of testing aspects of
the software system that has dependencies with adafruit libraries, given
the fact that the docker image being used for the CI/CD jobs that
perform unit testing and code coverage reporting are not pre-configured
with the required libraries to execute the tests.

As a proof-of-concept for proper unit testing and code coverage
reporting in the project's pipeline, this is the project that is being
used by the pipeline (see [`.gitlab-ci.yml`](../../.gitlab-ci.yml)) to
demonstrate the execution of tests and code coverage reports in the
project's CI/CD pipeline.

## Creating a test project

To create a test project, make a new directory for the project, and
paste in the contents of the `generic_testing` folder into the newly
made directory. The contents of the `generic_testing` project should be
sufficient for a barebones PIO project. Once the test project has been
made, development on the test project can begin.

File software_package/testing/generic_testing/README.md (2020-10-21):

# Installed Packages
```bash
'Adafruit BusIO'/
'Adafruit GFX Library'/
'Adafruit MPU6050'/
'Adafruit SSD1306'/
'Adafruit Unified Sensor'/
'FatFs'/
'STM32duino STM32SD'/
```

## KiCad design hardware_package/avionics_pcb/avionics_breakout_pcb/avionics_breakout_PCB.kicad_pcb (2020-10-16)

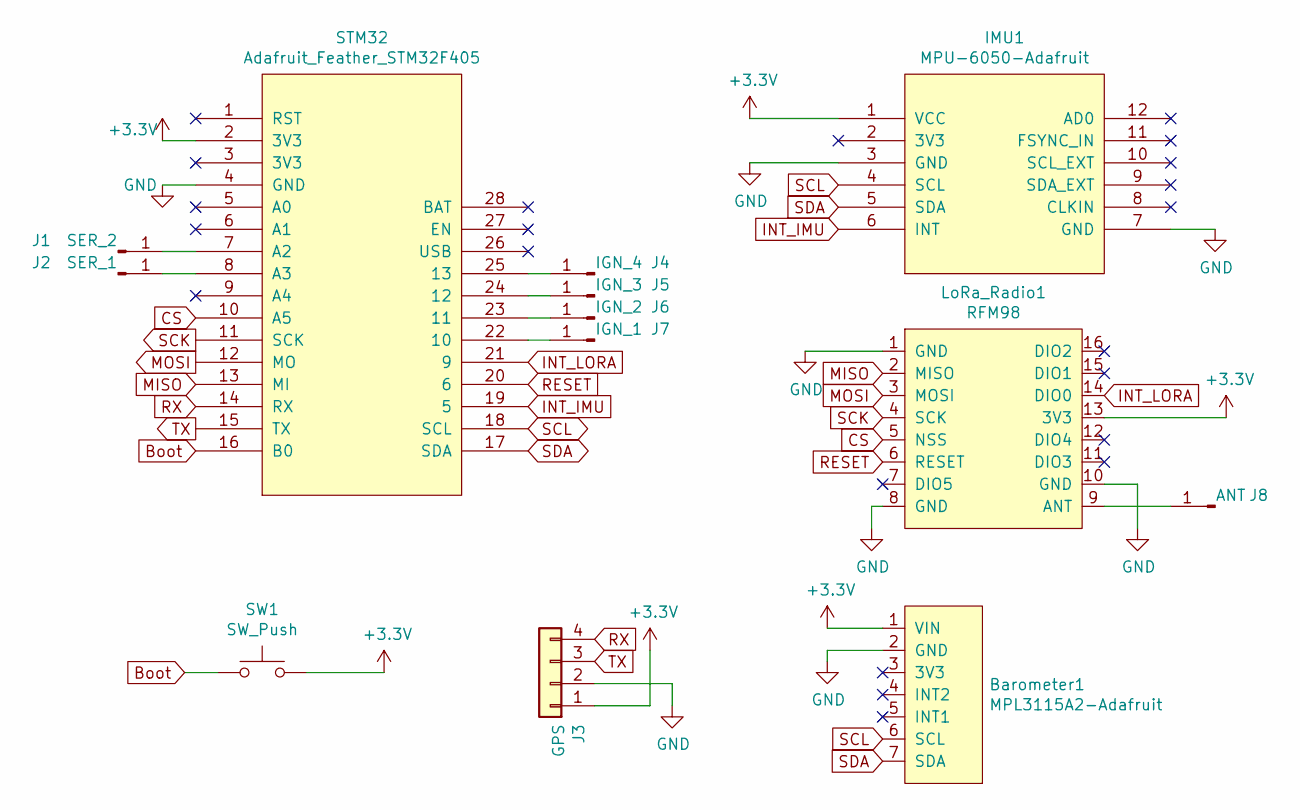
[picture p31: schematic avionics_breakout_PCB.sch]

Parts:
Barometer1: MPL3115A2-Adafruit
IMU1: MPU-6050-Adafruit; MPU6050-adafruit
J1: SER_2; SolderWire-0.1sqmm_1x01_D0.4mm_OD1mm
J2: SER_1; SolderWire-0.1sqmm_1x01_D0.4mm_OD1mm
J3: GPS; PinHeader_1x04_P2.54mm_Vertical
J4: IGN_4; SolderWire-0.1sqmm_1x01_D0.4mm_OD1mm
J5: IGN_3; SolderWire-0.1sqmm_1x01_D0.4mm_OD1mm
J6: IGN_2; SolderWire-0.1sqmm_1x01_D0.4mm_OD1mm
J7: IGN_1; SolderWire-0.1sqmm_1x01_D0.4mm_OD1mm
J8: ANT; SolderWire-0.1sqmm_1x01_D0.4mm_OD1mm
LoRa_Radio1: RFM98
STM32: Adafruit_Feather_STM32F405
SW1: SW_Push; SW_PUSH_6mm

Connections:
+3V3: Barometer1.1 (VIN), IMU1.1 (VCC), J3.1, LoRa_Radio1.13 (3V3), STM32.2 (3V3), SW1.2
Boot: STM32.16 (B0), SW1.1
CS: LoRa_Radio1.5 (NSS), STM32.10 (A5)
GND: Barometer1.2 (GND), IMU1.3 (GND), IMU1.7 (GND), J3.2, LoRa_Radio1.1 (GND), LoRa_Radio1.8 (GND), LoRa_Radio1.10 (GND), STM32.4 (GND)
INT_IMU: IMU1.6 (INT), STM32.19 (5)
INT_LORA: LoRa_Radio1.14 (DIO0), STM32.21 (9)
MISO: LoRa_Radio1.2 (MISO), STM32.13 (MI)
MOSI: LoRa_Radio1.3 (MOSI), STM32.12 (MO)
unnamed: J1.1, STM32.7 (A2)
unnamed: J2.1, STM32.8 (A3)
unnamed: J4.1, STM32.25 (13)
unnamed: J5.1, STM32.24 (12)
unnamed: J6.1, STM32.23 (11)
unnamed: J7.1, STM32.22 (10)
unnamed: J8.1, LoRa_Radio1.9 (ANT)
RESET: LoRa_Radio1.6 (RESET), STM32.20 (6)
RX: J3.4, STM32.14 (RX)
SCK: LoRa_Radio1.4 (SCK), STM32.11 (SCK)
SCL: Barometer1.6 (SCL), IMU1.4 (SCL), STM32.18 (SCL)
SDA: Barometer1.7 (SDA), IMU1.5 (SDA), STM32.17 (SDA)
TX: J3.3, STM32.15 (TX)

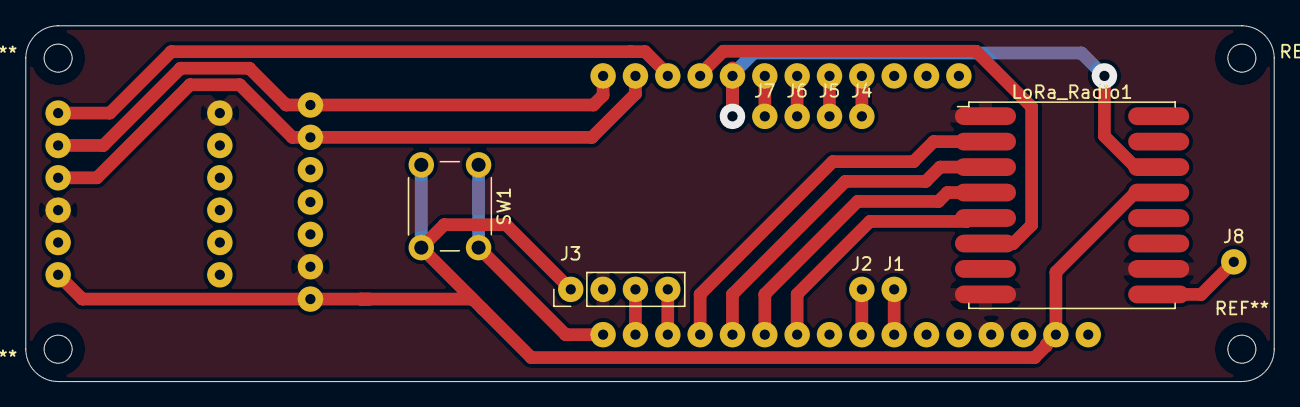
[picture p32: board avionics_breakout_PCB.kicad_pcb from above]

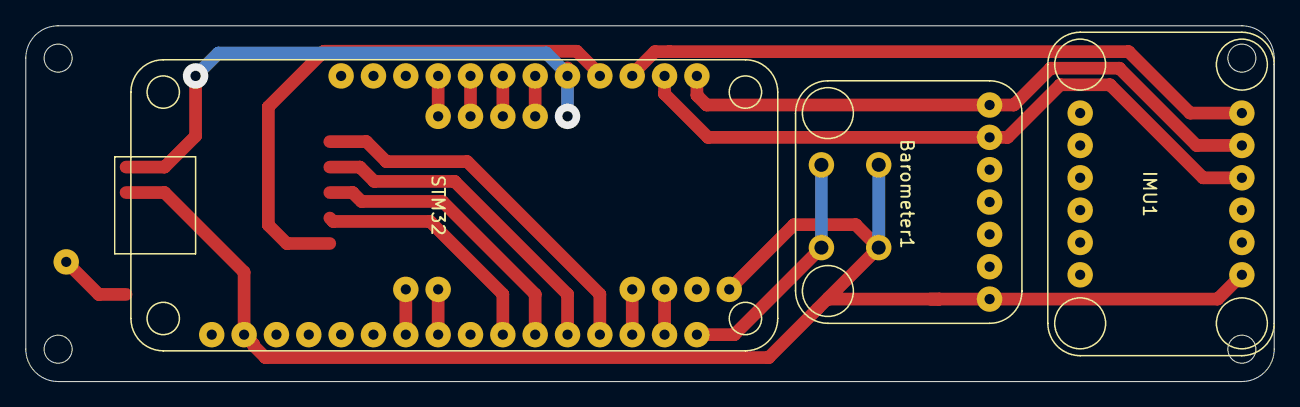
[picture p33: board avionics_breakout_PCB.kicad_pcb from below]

Board: 2 copper layers, 98.0 x 27.9 mm, 13 parts (3 on the bottom side), 21 nets.

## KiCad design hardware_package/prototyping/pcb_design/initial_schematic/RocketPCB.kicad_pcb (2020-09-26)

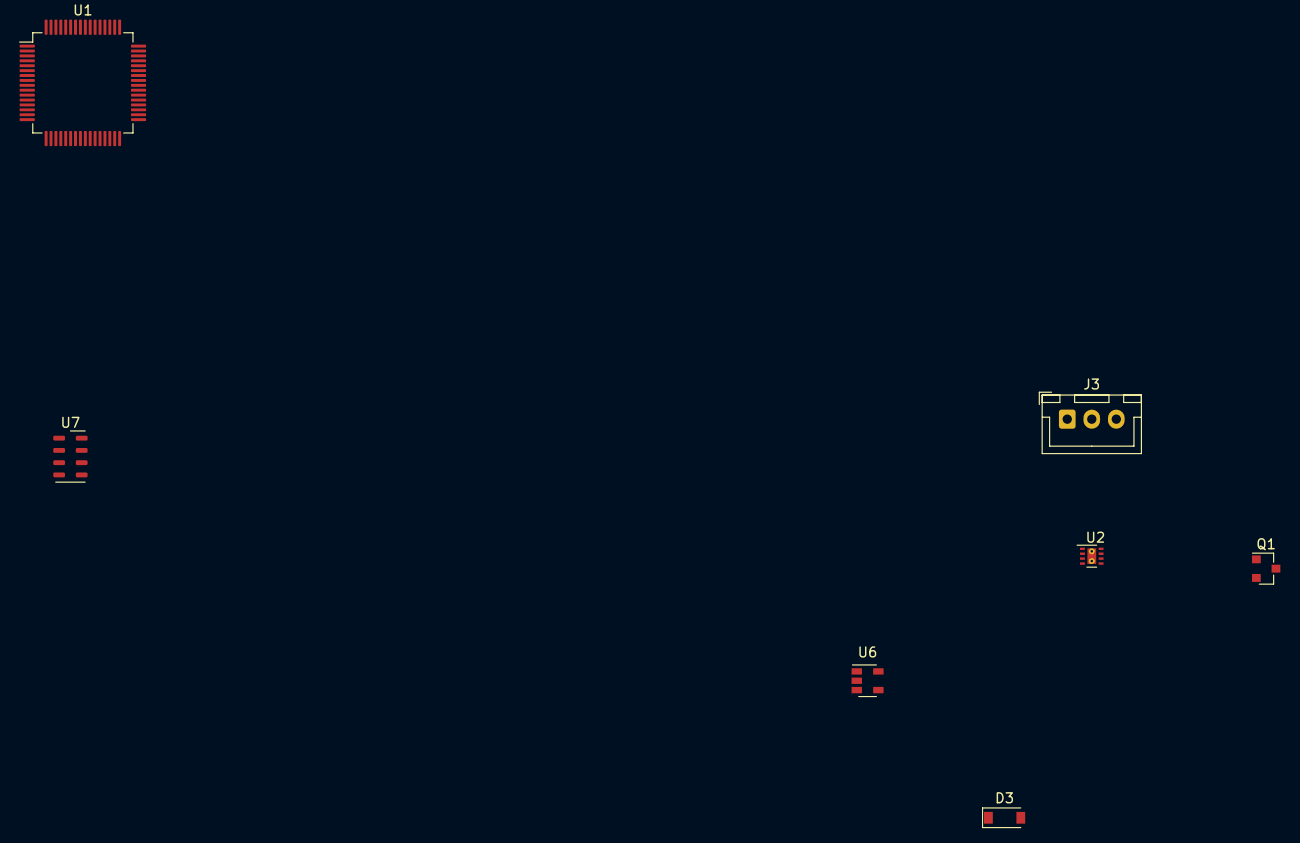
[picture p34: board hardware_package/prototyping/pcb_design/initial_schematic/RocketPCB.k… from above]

Board: 2 copper layers, 7 parts (0 on the bottom side), 10 nets, no tracks yet.

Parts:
D3: MBR0540; D_SOD-123
J3: Conn_01x03_Female; JST_XH_B3B-XH-A_1x03_P2.50mm_Vertical
Q1: DMG2301L; SOT-23
U1: STM32F405RGTx; LQFP-64_10x10mm_P0.5mm
U2: TPS62160DSG; WSON-8-1EP_2x2mm_P0.5mm_EP0.9x1.6mm_ThermalVias
U6: AP2112K-3.3; SOT-23-5
U7: MPL3115A2; NXP_LGA-8_3x5mm_P1.25mm_H1.1mm

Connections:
+3V3: U1.19, U1.32, U1.42, U1.43, U1.48, U1.64, U6.5, U7.1, U7.4
+7.5V: J3.3, U2.2, U2.3
/INT1: U1.22, U7.6
/INT2: U1.21, U7.5
/SCL: U1.58, U7.8
/SDA: U1.59, U7.7
GND: J3.1, U1.12, U1.18, U1.28, U1.63, U2.1, U2.4, U2.9, U6.2, U7.3
unnamed: D3.1, Q1.2, U6.1
TP3: Q1.3, U1.1, U2.6
VBUS: D3.2, Q1.1

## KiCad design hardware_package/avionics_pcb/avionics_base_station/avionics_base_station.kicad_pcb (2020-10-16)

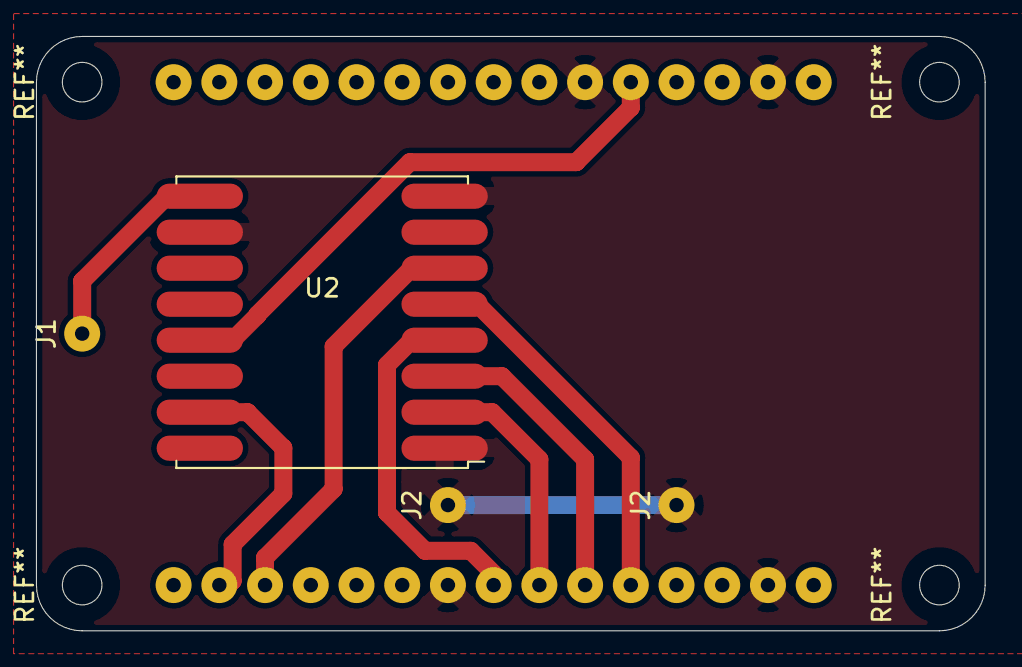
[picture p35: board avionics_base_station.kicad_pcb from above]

Board: 2 copper layers, 52.7 x 33.0 mm, 5 parts (1 on the bottom side), 9 nets.

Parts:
J1: ANT; SolderWire-0.1sqmm_1x01_D0.4mm_OD1mm
J2, J2#2: GND_PASS; SolderWire-0.1sqmm_1x01_D0.4mm_OD1mm
U1: NODEMCU
U2: RFM98

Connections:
+3V3: U1.20, U2.13
GND: J2.1, J2#2.1, U1.2, U1.9, U1.17, U1.21, U2.1, U2.8, U2.10
INT: U1.14, U2.15
MISO: U1.7, U2.2
MOSI: U1.6, U2.3
NSS: U1.5, U2.5
unnamed: J1.1, U2.9
RESET: U1.13, U2.6
SCK: U1.8, U2.4

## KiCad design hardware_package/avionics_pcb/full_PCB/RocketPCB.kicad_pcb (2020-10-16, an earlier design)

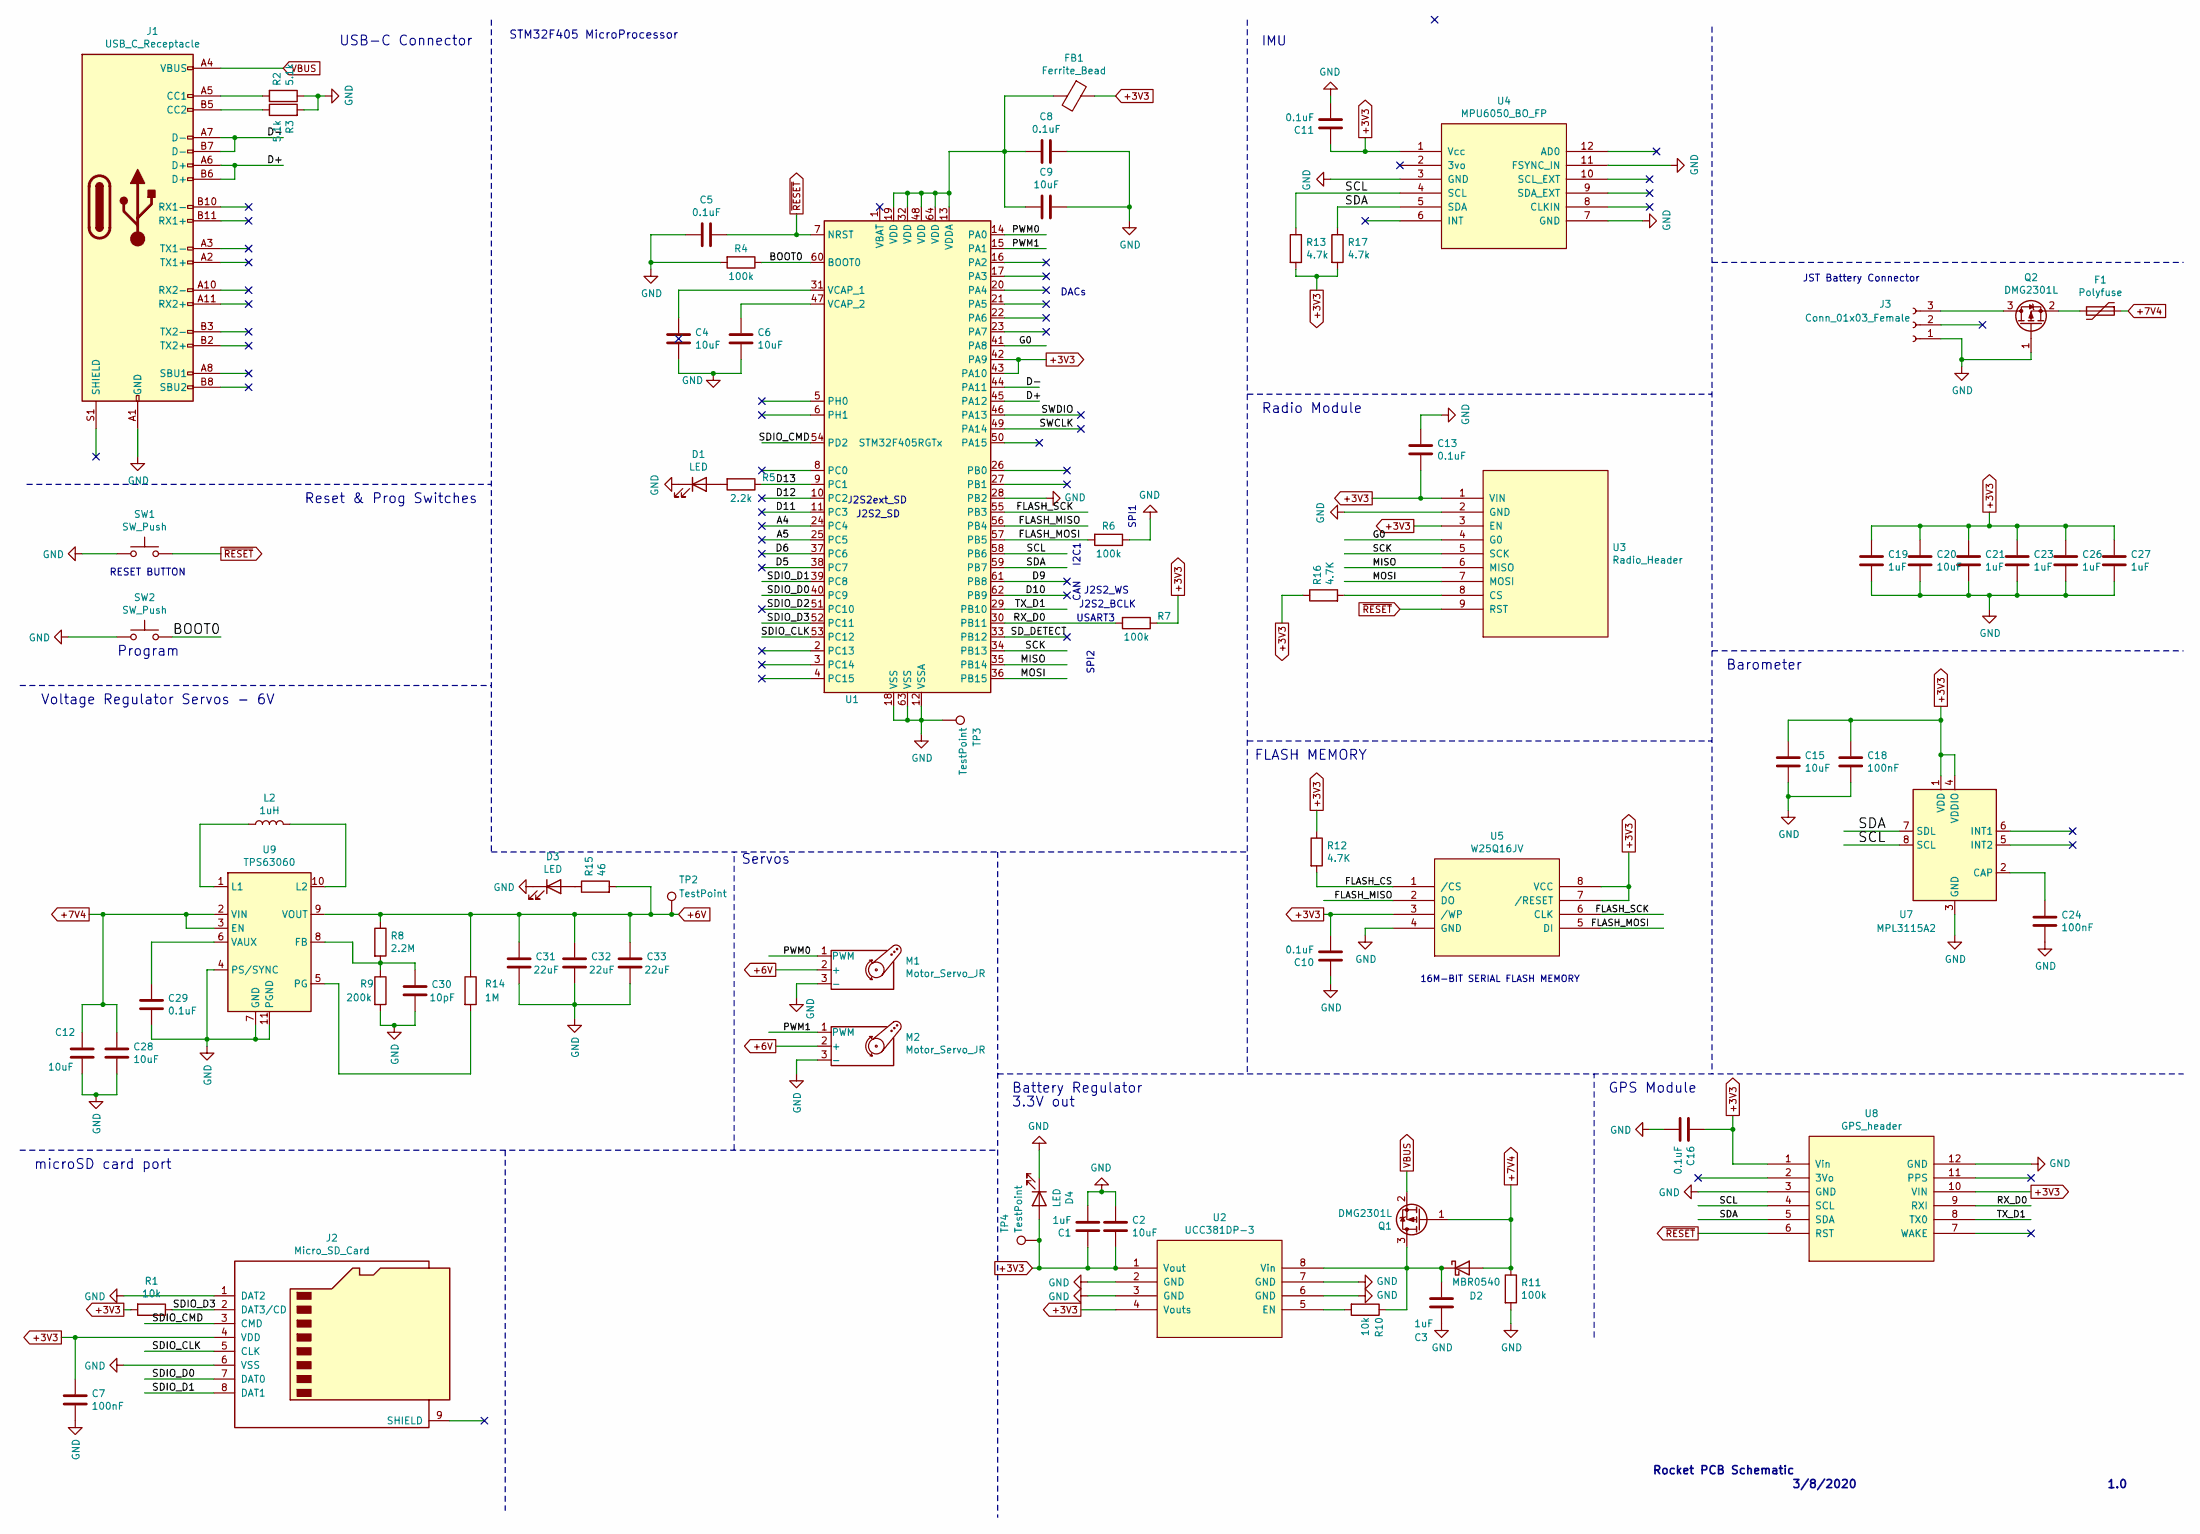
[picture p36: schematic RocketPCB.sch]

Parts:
C1, C3, C19, C21, C23, C26, C27: 1uF; C_0603_1608Metric
C2, C4, C6, C9, C12, C15, C20, C28: 10uF; C_0805_2012Metric
C5, C8, C10, C11, C13, C16, C29: 0.1uF; C_0603_1608Metric
C7, C18, C24: 100nF; C_0603_1608Metric
C30: 10pF; C_0603_1608Metric
C31, C32, C33: 22uF; C_0805_2012Metric
D1, D3, D4: LED; LED_0603_1608Metric_Pad1.05x0.95mm_HandSolder
D2: MBR0540; D_SOD-123
F1: Polyfuse; Fuse_Littelfuse_395Series
FB1: Ferrite_Bead; R_0402_1005Metric
J1: USB_C_Receptacle; USB_C_Receptacle_Palconn_UTC16-G
J2: Micro_SD_Card; microSD_HC_Hirose_DM3BT-DSF-PEJS
J3: Conn_01x03_Female; JST_XH_B3B-XH-A_1x03_P2.50mm_Vertical
L2: 1uH; L_0805_2012Metric
M1, M2: Motor_Servo_JR; JR_servo_connector
Q1, Q2: DMG2301L; SOT-23
R1, R10: 10k; R_0603_1608Metric
R2, R3: 5.1k; R_0603_1608Metric
R4, R6, R7, R11: 100k; R_0603_1608Metric
R5: 2.2k; R_0603_1608Metric
R8: 2.2M; R_0603_1608Metric
R9: 200k; R_0603_1608Metric
R12, R16: 4.7K; R_0603_1608Metric
R13, R17: 4.7k; R_0603_1608Metric
R14: 1M; R_0603_1608Metric
R15: 46; R_0603_1608Metric
SW1, SW2: SW_Push; SW_Push_SPST_NO_Alps_SKRK
TP2, TP3, TP4: TestPoint; TestPoint_Pad_D1.0mm
U1: STM32F405RGTx; LQFP-64_10x10mm_P0.5mm
U2: UCC381DP-3; SOIC127P599X175-8N
U3: Radio_Header; gps_header_footprint
U4: MPU6050_BO_FP; MPU6050-footprint
U5: W25Q16JV; W25Q16JV_footprint
U7: MPL3115A2; NXP_LGA-8_3x5mm_P1.25mm_H1.1mm
U8: GPS_header; GPS_header_fp
U9: TPS63060; Texas_S-PWSON-N10_ThermalVias

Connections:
+3V3: C1.1, C2.2, C7.1, C10.2, C11.1, C13.2, C15.1, C16.1, C18.1, C19.1, C20.1, C21.1, C23.1, C26.1, C27.1, D4.2 (A), FB1.1, J2.4 (VDD), R1.2, R7.1, R12.1, R13.2, R16.1, R17.2, TP4.1, U1.42 (PA9), U1.43 (PA10), U2.1 (Vout), U2.4 (Vouts), U3.1 (VIN), U3.3 (EN), U4.1 (Vcc), U5.3 (/WP), U5.7 (/RESET), U5.8 (VCC), U7.1 (VDD), U7.4 (VDDIO), U8.1 (Vin), U8.10 (VIN)
+6V: C31.1, C32.1, C33.1, M1.2 (+), M2.2 (+), R8.1, R14.1, R15.2, TP2.1, U9.9 (VOUT)
+7V4: C12.1, C28.1, D2.2 (A), F1.1, Q1.1 (G), R11.1, U9.2 (VIN), U9.3 (EN)
/A4: U1.24 (PC4)
/A5: U1.25 (PC5)
/BOOT0: R4.1, SW2.2, U1.60 (BOOT0)
/D5: U1.38 (PC7)
/D6: U1.37 (PC6)
/D9: U1.61 (PB8)
/D10: U1.62 (PB9)
/D11: U1.11 (PC3)
/D12: U1.10 (PC2)
/D13: R5.1, U1.9 (PC1)
/D+: J1.A6 (D+), J1.B6 (D+), U1.45 (PA12)
/D-: J1.A7 (D-), J1.B7 (D-), U1.44 (PA11)
/FLASH_CS: R12.2, U5.1 (/CS)
/FLASH_MISO: U1.56 (PB4), U5.2 (DO)
/FLASH_MOSI: R6.2, U1.57 (PB5), U5.5 (DI)
/FLASH_SCK: U1.55 (PB3), U5.6 (CLK)
/G0: U1.41 (PA8), U3.4 (G0)
/MISO: U1.35 (PB14), U3.6 (MISO)
/MOSI: U1.36 (PB15), U3.7 (MOSI)
/PWM0: M1.1 (PWM), U1.14 (PA0)
/PWM1: M2.1 (PWM), U1.15 (PA1)
/RX_D0: R7.2, U1.30 (PB11), U8.9 (RXI)
/SCK: U1.34 (PB13), U3.5 (SCK)
/SCL: R13.1, U1.58 (PB6), U4.4 (SCL), U7.8 (SCL), U8.4 (SCL)
/SDA: R17.1, U1.59 (PB7), U4.5 (SDA), U7.7 (SDL), U8.5 (SDA)
/SDIO_CLK: J2.5 (CLK), U1.53 (PC12)
/SDIO_CMD: J2.3 (CMD), U1.54 (PD2)
/SDIO_D0: J2.7 (DAT0), U1.40 (PC9)
/SDIO_D1: J2.8 (DAT1), U1.39 (PC8)
/SDIO_D2: U1.51 (PC10)
/SDIO_D3: J2.2 (DAT3/CD), R1.1, U1.52 (PC11)
/SD_DETECT: U1.33 (PB12)
/SWCLK: U1.49 (PA14)
/SWDIO: U1.46 (PA13)
/TX_D1: U1.29 (PB10), U8.8 (TX0)
GND: C1.2, C2.1, C3.2, C4.2, C5.1, C6.2, C7.2, C8.2, C9.2, C10.1, C11.2, C12.2, C13.1, C15.2, C16.2, C18.2, C19.2, C20.2, C21.2, C23.2, C24.2, C26.2, C27.2, C28.2, C29.2, C30.2, C31.2, C32.2, C33.2, D1.1 (K), D3.1 (K), D4.1 (K), J1.A1 (GND), J1.A12 (GND), J1.B1 (GND), J1.B12 (GND), J2.1 (DAT2), J2.6 (VSS), J3.1, M1.3 (-), M2.3 (-), Q2.1 (G), R2.1, R3.2, R4.2, R6.1, R9.2, R11.2, SW1.1, SW2.1, TP3.1, U1.12 (VSSA), U1.18 (VSS), U1.28 (PB2), U1.63 (VSS), U2.2 (GND), U2.3 (GND), U2.6 (GND), U2.7 (GND), U3.2 (GND), U4.3 (GND), U4.7 (GND), U4.11 (FSYNC_IN), U5.4 (GND), U7.3 (GND), U8.3 (GND), U8.12 (GND), U9.4 (PS/SYNC), U9.7 (GND), U9.11 (PGND)
unnamed: C3.1, D2.1 (K), Q1.3 (D), R10.1, U2.8 (Vin)
unnamed: C4.1, U1.31 (VCAP_1)
unnamed: C6.1, U1.47 (VCAP_2)
unnamed: C8.1, C9.1, FB1.2, U1.13 (VDDA), U1.19 (VDD), U1.32 (VDD), U1.48 (VDD), U1.64 (VDD)
unnamed: C24.1, U7.2 (CAP)
unnamed: C29.1, U9.6 (VAUX)
unnamed: C30.1, R8.2, R9.1, U9.8 (FB)
unnamed: D1.2 (A), R5.2
unnamed: D3.2 (A), R15.1
unnamed: F1.2, Q2.2 (S)
unnamed: J1.A5 (CC1), R2.2
unnamed: J1.B5 (CC2), R3.1
unnamed: J3.3, Q2.3 (D)
unnamed: L2.1, U9.1 (L1)
unnamed: L2.2, U9.10 (L2)
unnamed: R10.2, U2.5 (EN)
unnamed: R14.2, U9.5 (PG)
unnamed: R16.2, U3.8 (CS)
VBUS: J1.A4 (VBUS), J1.A9 (VBUS), J1.B4 (VBUS), J1.B9 (VBUS), Q1.2 (S)
~RESET~: C5.2, SW1.2, U1.7 (NRST), U3.9 (RST), U8.6 (RST)

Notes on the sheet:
DACs
RESET BUTTON
JST Battery Connector
USB-C Connector
Rocket PCB Schematic
3/8/2020
1.0
IMU
SPI2
USART3
J2S2_BCLK
J2S2_WS
CAN
SPI1
STM32F405 MicroProcessor
J2S2_SD
J2S2ext_SD
I2C1
microSD card port
Barometer
Program
Reset & Prog Switches
Battery Regulator
GPS Module
Radio Module
3.3V out
FLASH MEMORY
16M-BIT SERIAL FLASH MEMORY
Voltage Regulator Servos - 6V
Servos

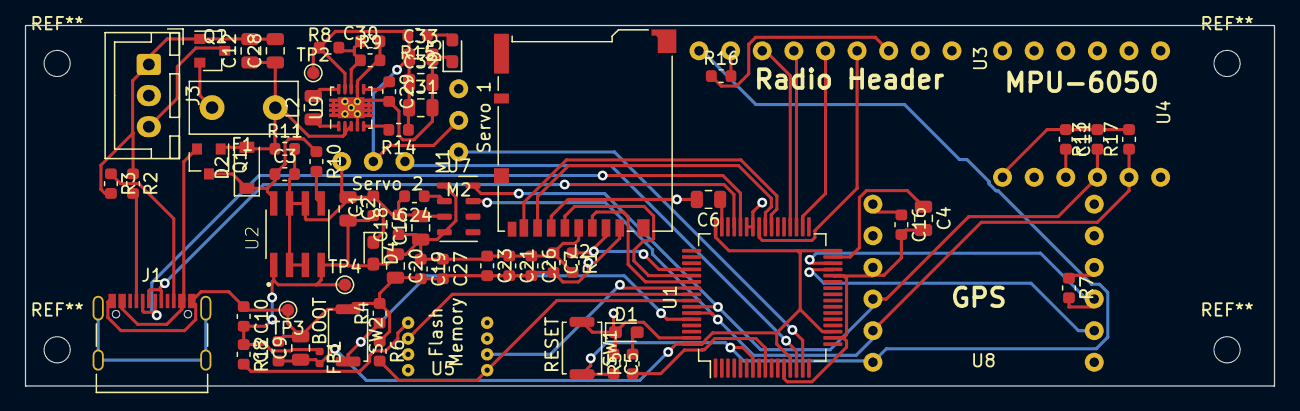
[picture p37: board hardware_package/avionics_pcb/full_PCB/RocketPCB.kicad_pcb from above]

Board: 4 copper layers, 100.3 x 29.0 mm, 72 parts (0 on the bottom side), 47 nets.

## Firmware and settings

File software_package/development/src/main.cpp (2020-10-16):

#include <Arduino.h>

#include <sstream>
#include <string>

/* Hardware Package */
#include "barometer.h"
#include "gservo.h"
#include "imu.h"
#include "lora.h"
#include "parachute.h"
#include "sd.h"

/* Software Package */
#include "debug.h"
#include "guidance.h"
#include "logging.h"
// #include "guidance_pid.h"

GuidanceSystem guidance;
Barometer baro;
Logging logger;
unsigned int counter;

void setup() {
  // put your setup code here, to run once:
  DEBUG_MSG_LN(1, "Beginning global setup.");

  guidance.init();
  baro.init();

  DEBUG_MSG_LN(1, "Finished global setup, beginning main loop.");
}

void loop() {
  // put your main code here, to run repeatedly:
  guidance.step();

  // optional logging.
  if (DEBUG > 2) {
    if (++counter % 30) {
      std::stringstream ss;
      ss << "alt: " << baro.read_altitude() << "m" << std::endl;
      logger.log_sd(ss.str());
    }

    if (counter % 60) {
      logger.flush_sd();
    }
  }
}

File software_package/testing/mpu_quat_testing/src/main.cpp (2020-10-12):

// I2C device class (I2Cdev) demonstration Arduino sketch for MPU6050 class using DMP (MotionApps v2.0)
// 6/21/2012 by Jeff Rowberg <jeff@rowberg.net>
// Updates should (hopefully) always be available at https://github.com/jrowberg/i2cdevlib
//
// Changelog:
//      2019-07-08 - Added Auto Calibration and offset generator
//		   - and altered FIFO retrieval sequence to avoid using blocking code
//      2016-04-18 - Eliminated a poitential infinite loop
//      2013-05-08 - added seamless Fastwire support
//                 - added note about gyro calibration
//      2012-06-21 - added note about Arduino 1.0.1 + Leonardo compatibility error
//      2012-06-20 - improved FIFO overflow handling and simplified read process
//      2012-06-19 - completely rearranged DMP initialization code and simplification
//      2012-06-13 - pull gyro and accel data from FIFO packet instead of reading directly
//      2012-06-09 - fix broken FIFO read sequence and change interrupt detection to RISING
//      2012-06-05 - add gravity-compensated initial reference frame acceleration output
//                 - add 3D math helper file to DMP6 example sketch
//                 - add Euler output and Yaw/Pitch/Roll output formats
//      2012-06-04 - remove accel offset clearing for better results (thanks Sungon Lee)
//      2012-06-01 - fixed gyro sensitivity to be 2000 deg/sec instead of 250
//      2012-05-30 - basic DMP initialization workng

/* ============================================
I2Cdev device library code is placed under the MIT license
Copyright (c) 2012 Jeff Rowberg

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
THE SOFTWARE IS PROVIDED "AS IS", WITHOUT WARRANTY OF ANY KIND, EXPRESS OR
IMPLIED, INCLUDING BUT NOT LIMITED TO THE WARRANTIES OF MERCHANTABILITY,
FITNESS FOR A PARTICULAR PURPOSE AND NONINFRINGEMENT. IN NO EVENT SHALL THE
AUTHORS OR COPYRIGHT HOLDERS BE LIABLE FOR ANY CLAIM, DAMAGES OR OTHER
LIABILITY, WHETHER IN AN ACTION OF CONTRACT, TORT OR OTHERWISE, ARISING FROM,
OUT OF OR IN CONNECTION WITH THE SOFTWARE OR THE USE OR OTHER DEALINGS IN
THE SOFTWARE.
===============================================
*/

// I2Cdev and MPU6050 must be installed as libraries, or else the .cpp/.h files
// for both classes must be in the include path of your project
#include <Arduino.h>
#include "I2Cdev.h"

#include "MPU6050_6Axis_MotionApps20.h"
//#include "MPU6050.h" // not necessary if using MotionApps include file

// Arduino Wire library is required if I2Cdev I2CDEV_ARDUINO_WIRE implementation
// is used in I2Cdev.h
#if I2CDEV_IMPLEMENTATION == I2CDEV_ARDUINO_WIRE
    #include "Wire.h"
#endif

// class default I2C address is 0x68
// specific I2C addresses may be passed as a parameter here
// AD0 low = 0x68 (default for SparkFun breakout and InvenSense evaluation board)
// AD0 high = 0x69
MPU6050 mpu;
//MPU6050 mpu(0x69); // <-- use for AD0 high

/* =========================================================================
   NOTE: In addition to connection 3.3v, GND, SDA, and SCL, this sketch
   depends on the MPU-6050's INT pin being connected to the Arduino's
   external interrupt #0 pin. On the Arduino Uno and Mega 2560, this is
   digital I/O pin 2.
 * ========================================================================= */

/* =========================================================================
   NOTE: Arduino v1.0.1 with the Leonardo board generates a compile error
   when using Serial.write(buf, len). The Teapot output uses this method.
   The solution requires a modification to the Arduino USBAPI.h file, which
   is fortunately simple, but annoying. This will be fixed in the next IDE
   release. For more info, see these links:

   http://arduino.cc/forum/index.php/topic,109987.0.html
   http://code.google.com/p/arduino/issues/detail?id=958
 * ========================================================================= */



// uncomment "OUTPUT_READABLE_QUATERNION" if you want to see the actual
// quaternion components in a [w, x, y, z] format (not best for parsing
// on a remote host such as Processing or something though)
#define OUTPUT_READABLE_QUATERNION

// uncomment "OUTPUT_READABLE_EULER" if you want to see Euler angles
// (in degrees) calculated from the quaternions coming from the FIFO.
// Note that Euler angles suffer from gimbal lock (for more info, see
// http://en.wikipedia.org/wiki/Gimbal_lock)
//#define OUTPUT_READABLE_EULER

// uncomment "OUTPUT_READABLE_YAWPITCHROLL" if you want to see the yaw/
// pitch/roll angles (in degrees) calculated from the quaternions coming
// from the FIFO. Note this also requires gravity vector calculations.
// Also note that yaw/pitch/roll angles suffer from gimbal lock (for
// more info, see: http://en.wikipedia.org/wiki/Gimbal_lock)
// #define OUTPUT_READABLE_YAWPITCHROLL

// uncomment "OUTPUT_READABLE_REALACCEL" if you want to see acceleration
// components with gravity removed. This acceleration reference frame is
// not compensated for orientation, so +X is always +X according to the
// sensor, just without the effects of gravity. If you want acceleration
// compensated for orientation, us OUTPUT_READABLE_WORLDACCEL instead.
//#define OUTPUT_READABLE_REALACCEL

// uncomment "OUTPUT_READABLE_WORLDACCEL" if you want to see acceleration
// components with gravity removed and adjusted for the world frame of
// reference (yaw is relative to initial orientation, since no magnetometer
// is present in this case). Could be quite handy in some cases.
//#define OUTPUT_READABLE_WORLDACCEL

// uncomment "OUTPUT_TEAPOT" if you want output that matches the
// format used for the InvenSense teapot demo
//#define OUTPUT_TEAPOT



#define INTERRUPT_PIN 2  // use pin 2 on Arduino Uno & most boards
#define LED_PIN 13 // (Arduino is 13, Teensy is 11, Teensy++ is 6)
bool blinkState = false;

// MPU control/status vars
bool dmpReady = false;  // set true if DMP init was successful
uint8_t mpuIntStatus;   // holds actual interrupt status byte from MPU
uint8_t devStatus;      // return status after each device operation (0 = success, !0 = error)
uint16_t packetSize;    // expected DMP packet size (default is 42 bytes)
uint16_t fifoCount;     // count of all bytes currently in FIFO
uint8_t fifoBuffer[64]; // FIFO storage buffer

// orientation/motion vars
Quaternion q;           // [w, x, y, z]         quaternion container
VectorInt16 aa;         // [x, y, z]            accel sensor measurements
VectorInt16 aaReal;     // [x, y, z]            gravity-free accel sensor measurements
VectorInt16 aaWorld;    // [x, y, z]            world-frame accel sensor measurements
VectorFloat gravity;    // [x, y, z]            gravity vector
float euler[3];         // [psi, theta, phi]    Euler angle container
float ypr[3];           // [yaw, pitch, roll]   yaw/pitch/roll container and gravity vector

// packet structure for InvenSense teapot demo
uint8_t teapotPacket[14] = { '$', 0x02, 0,0, 0,0, 0,0, 0,0, 0x00, 0x00, '\r', '\n' };
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

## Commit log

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2020-06-12 Replaces Power of 10 points with numbers for clarity.
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2020-06-19 Added: Battery, Prototype DC-DC supplys, New folder for Hardware files.
    [BOM.csv, Detailed_Operating_Values.csv, Detailed_Opertating_Values.csv]
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2020-06-19 Adds experimental markdown linter.
    This will need to be checked on Gitlab before merged!
    [KiCad.kicad_pcb, KiCad.sch]
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2020-06-19 Fixes C++ issues and adds a test file
    In this commit we fix any C++ violations ensuring all headers
    and files and compile using G++. In this commit, we also add a
    tests.cpp file. This creates objects from all of the classes
    declared within the package. This also runs their methods to
    ensure that there are no errors present. In the future, we will
    focus on researching into unit testing frameworks for C++. To
    help build, lint and compile the tests a bash script run_tests.sh
    has been added. This requires the user has cpplint and gcc
    installed on the system
2020-06-19 reformatted the hardware directory, added final bill of materials
    [BOM.csv, bill_of_materials.csv, detailed_operating_values.csv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]
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2020-06-25 Reformatted hardware directories, making the repository cleaner. Final update of the BOM
    [BOM.csv, bill_of_materials.csv, detailed_operating_values.csv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]
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2020-07-06 disconnected pad from PCB, testing if the pipeline works correctly
    [KiCad.kicad_pcb]
2020-07-06 Connected pad to PCB, testing if the pipeline works correctly
    [KiCad.kicad_pcb]
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2020-07-24 Refactors software package to comply with Platformio.
    In this commit, we add a working main cpp file that runs on the board (Credit to
    Niels on getting this working). We shuffle around the existing files to better comply
    with the recommended directory structures. We also add an entry the the .gitlab-ci.yml
    which should hopefully be on the right track (but I suspect that there will be issues
    with this). We also add an example test file that follows the recommended structure and
    includes files from the control library. This is a work in progress, and a lot of the
    stuff is very finicky.
2020-07-24 Made sensors package compliant with cpplint
    Also includes the removal of random value generation for sensor readings (because apparently
    rand() is not thread safe and cpplint didn't like that)
    [main.cpp]
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2020-07-31 Configures the control package to run tests like the communication package
    In this commit, we change how we are calling the tests in the control suite to utilise the
    RUN_TEST() function built into Unity. This allows us to get more detailed output regarding
    which tests passed and failed as well as the error that occurred
    [test_control.cpp]
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2020-08-05 Creates Platformio subprojects
    In this commit we move the contents from the first
    project and move them into 2 different subprojects.
    We have a 'development' and 'testing' project. The
    development project is will contain all of the
    finalised code whereas the testing project will
    contain various methods to check whether the
    hardware is performing correctly.
    [main.cpp, test_control.cpp]
2020-08-05 Integrates SD card tests into Platformio Unit Testing
    In this commit we integrate Platformio Unit testing for the hardware level.
    This turns out to be pretty finicky and hasn't been figured out fully yet.
    When the tests begin executing, platformio will try upload the test files
    to the board. It will then invoke the tests and they will run one by one.
    However, the status of the tests is not displayed in the test window.
    Instead the user is prompted with 'If you don’t see any output for the first
    10 secs, please reset board (press reset button)'. To get around this for
    now we have to switch to the serial output perspective in platformio to
    read the test results of the hardware. For now how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
    [test_sd.cpp]
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2020-08-05 Added code-coverage job to .gitlab-ci.yml
    This commit also removes the 'job' job that falls under the Platformio
    stage. This is a temporary thing until we resolve why this job was
    failing.
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2020-08-05 Updated log, added prototype 1 and 2 directories.
    [Assembly 1.x_t, Bottom_Servo_Mount.x_t, Tube.x_t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]
2020-08-05 PSU design schematic (KiCad) and switching reg report
    [BOM.csv, detailed_operating_values.csv, detailed_opertating_values.csv]
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2020-08-05 Set up sensor package for testing environment. Fixed header issues.
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2020-08-06 Circuit Schematic w chip, SD card, USB, Power, Filter, Reset & 3.3V reg
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2020-08-10 Reads data from the Barometer.
    The code now can read data from the Barometer. At the moment,
    sadly this is reading an altitude of 25k meters above Sea level.
    As we are breathing I suspect there might be something wrong with
    how things are setup at the moment.
    [main.cpp]
2020-08-10 Correct readings for altitude by commenting out the read temp line.
    See more on the official page: https://github.com/adafruit/Adafruit_MPL3115A2_Library/issues/16
    [main.cpp]
2020-08-18 Updated code-coverage job and code coverage script
    This commit updates the code-coverage CI/CD job to work with the new
    version of the code coverage generation script. It also GitLab code
    coverage parsing (see #121 for details) to enable GitLab to show % of
    lines covered
    This commit also sees a minor overhaul to the code coverage generation
    script. The script now uses flags '-f' and '-t' to allow someone to
    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
    [Assembly 1 2.x_t, Bottom_Servo_Mount 2.x_t, KiCad 2.kicad_pcb]
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2020-08-21 Created an assembly, may need to make adjustments for bolts in future.
    [assembly_1.x_t]
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2020-09-03 SD card refactored successfully (hopefully).
    Finn and I refactored the SD logic into the library
    files. We encountered a plethora of issues along the
    way but it appears to be compiling and running on the
    rocket. Hopefully we can follow this structure for the
    rest of the code.
    [main.cpp]
2020-09-06 Refactors IMU into new hardware libraries
    In this commit, we refactor the IMU code into the new
    libraries. We also fix a couple compiler warnings (would
    have lead to memory leak) within the SD logic and tidy
    up the main.cpp file. We also provide a simple example
    of how it should be used including initialisation and
    within loop().
    [main.cpp]
2020-09-06 Fixes architecture-design.md post merge.
    In this commit we fix up the architecture-design conflicts after the merge. We ensure that the document now
    passes the linter as best we can (as well as fix a couple typos and missing figure clauses.
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2020-09-07 Tests the code on the rocket hardware.
    In this commit, we test the code on the hardware and
    fix any of the issues that we were encountering. One
    of the notable bugs that we had to fix was the Arduino
    `printf` function does not support `%f`. Unfortunately,
    due to issues with the SD card we are not able to verify
    whether it is working as intended. The barometer is also
    reading out slightly incorrect values, however the way
    that we are interacting with it has not been changing.
    [main.cpp]
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2020-09-11 Several components have been created, the gimbal has been revised.
    [BodyTube.x_t, pcb.x_t]
2020-09-14 Implements template for PID controller.
    In this commit, we create a compiling template
    for the PID controller functionality of the rocket.
    We introduce an inner class containing the basis of
    PID functionality. For each of these, they act as a
    wrapper around a Servo component. Each of these will
    be called to step and handle both the X and Y axis
    servos individually upon GuidanceSystem::step_pid().
    HELP: I seem to be getting quite a few issues
    regarding initializing the PID objects (relating
    to deleted function). I will need to do more reading
    into this, I assume this will automatically be
    initialized if I cannot manually perform this action?
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2020-09-15 Setup of PCB for prototype 1, includes headers for breakout boards.
    [Adafruit PA1010D Mini GPS.sch, PCBwBreakout.kicad_pcb, PCBwBreakout.sch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]
2020-09-15 Fixed Schematic frame & title, added Lora Headers
    [PCBwBreakout.sch]
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2020-09-15 Added MP3115A2 Header, made custom 1X7 Header symbol
    [PCBwBreakout.sch]
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2020-09-16 Introduces imu and parachute into Guidance System PID.
    In this commit we introduce the imu and parachute components
    into the guidance system. We also fix some extra logic such
    as passing rocket angle into function instead of pid value.
    (silly me).
2020-09-16 Renames test project directories, tidies code to meet project code style guide.
    In this commit, we make a couple minor changes. Firstly we rename the testing
    project folder names to match the rest of the project structure and naming
    conventions. We also tidy the introduced main.cpp C++ code to touch up any
    spelling mistakes and better comply with the Google Style Guide.
    [main.cpp]
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2020-09-17 Refoctor the hardware directory to move the PCB design to a single location, created footprints and symbols for each of the boards we will be adding to the PCB
    [Adafruit PA1010D Mini GPS.sch, PCBwBreakout.kicad_pcb, PCBwBreakout.sch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]
2020-09-17 Created the footprint libraries, and the symbol libraries for the breakout boards, made a start on the PCB routing and schematic
    [avionics_breakout_PCB.kicad_pcb, avionics_breakout_PCB.sch]
2020-09-17 Implemented state pattern
    This commit introduces some files to do with the state management of the
    rocket. Currently, there are 2 important concepts, The StateMachine
    class and the States class. The StateMachine construct serves the
    purpose of executing the actions that need to be undertaken in a
    specific state. State instances define a specific state the rocket can
    take, and the actions the rocket must perform while in that state.
    The advantage of implementing the state pattern to manage the state of
    the rocket is that it enables the rest of the software system to issue
    calls to the state machine to cause a change in state (eg in guidance
    system, a call can be made to a StateMachine instan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
2020-09-17 Completed the PCB for the breakout board based avionics board. Also updated the CI/CD to include this new PCB
    [KiCad 2.kicad_pcb, KiCad.kicad_pcb, KiCad.sch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]
2020-09-17 Fixed DRC check errors
    [avionics_breakout_PCB.kicad_pcb, avionics_breakout_PCB.sch]
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2020-09-18 Added servo data connections, as well as ingnition charge data lines
    [avionics_breakout_PCB.kicad_pcb, avionics_breakout_PCB.sch]
2020-09-18 Large commit. updated gimbal, added Andres rocket, still need modify it.
    [Assembly 1.x_t, BodyTube.x_t, Bottom_Servo_Mount.x_t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]
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2020-09-18 fixing values, connecting nets and removing redundant nets
    [RocketPCB.sch]
2020-09-19 Lora Base Station project setup, beginning the construction of the schematic
    [avionics_base_station.kicad_pcb, avionics_base_station.sch]
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2020-09-20 Editied titles and boundaries to tidy up layout
    [RocketPCB.sch]
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2020-09-26 Finished the new PCB layout for the breakout avionics PCB
    [avionics_breakout_PCB.kicad_pcb, avionics_breakout_PCB.sch]
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2020-09-27 Added test_environment_experiment PIO project
    The purpose of this PIO project is to serve as a clean playground to
    enable the exploration of PIO and its unit testing capabilities without
    damaging the existing code base.
    It is likely that this PIO project will serve as the proof-of-concept
    with regards to our current unit testing for the entire project, as well
    as the code coverage stuff we have setup so far. This is because of the
    fact that this project is completely free from any adafruit libraries
    which has proven to be an obstacle in the tackling of this issue.
    [main.cpp]
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2020-09-30 Removed redundant directory and updated the gimbal progress log
    [Assembly 1 2.x_t, Bottom_Servo_Mount 2.x_t]
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2020-09-30 Added most of the foot prints inc. R, C, I, LEDs etc
    [RocketPCB.csv, RocketPCB.kicad_pcb, RocketPCB.sch]
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2020-09-30 Update the avionics breakout PCB and schematic. These updates have made the schematic more readable, and will be used for screenshots within the readme
    [avionics_breakout_PCB.kicad_pcb, avionics_breakout_PCB.sch]
2020-10-03 Assigned additional footprints adding headers for radio and GPS
    [RocketPCB.sch]
2020-10-03 Added all FPs some issues still, +safety features and regulator
    [RocketPCB.sch]
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2020-10-05 Refactored the PCB and schematic to be placed in a readme. Also created a readme for the Base Station PCB, and added the images
    [avionics_base_station.kicad_pcb, avionics_base_station.sch]
2020-10-05 Removed the redundant PCBwBreakout directory, as it is not required or used
    [PCBwBreakout.kicad_pcb, PCBwBreakout.sch]
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2020-10-06 Adds mpu_servo_testing project to map mpu readings to servo.
    In this commit, we add another test project where we map the
    readings from the MPU (using the i2cdev and mpu-i2cdev) libraries.
    Although we were having success with the green servo,
    unfortunately the wiring has frayed on the pink servo causing
    shorting meaning that we could not test it.
    [main.cpp]
2020-10-06 Started laying out PCB added 6V reg to schematic
    [RocketPCB.csv, RocketPCB.kicad_pcb, RocketPCB.sch]
2020-10-06 Removed additional oscillators.
    [RocketPCB.sch]
2020-10-07 Combined two of the regulators, reassigned footprints, added pull up R
    [RocketPCB.sch]
2020-10-10 Added test points and LEDs for debug, also added decoupling capacitors
    [RocketPCB.kicad_pcb, RocketPCB.sch]
2020-10-11 Fixed IMU, USB & JR conn fp/p/o conflict, laid out PCB blocks
    [RocketPCB.kicad_pcb]
2020-10-11 Made gimbal P4 - final prototype model and updated documentation and directories.
    [Assembly.x_t, BodyTube.x_t, assembly.x_t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]
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2020-10-11 Modified to 4 layer PCB, laid out 6V and 3V3 regulators
    [RocketPCB.sch]
2020-10-11 Laid out and routed the majority of the board
    [RocketPCB.kicad_pcb, RocketPCB.sch]
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2020-10-12 Finished routing and laying out first iteration of final PCB
    [RocketPCB.kicad_pcb]
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2020-10-13 Updated with the correct version
    [RocketPCB.kicad_pcb, RocketPCB.sch]
2020-10-13 Labelled reset/boot buttons
    [RocketPCB.kicad_pcb]
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2020-10-16 Added mounting holes to PCB, small schem edits and moved USB-C port
    [Adafruit PA1010D Mini GPS.sch, RocketPCB.csv, RocketPCB.kicad_pcb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]
2020-10-16 modelled PCB fixture added to whole model. Updated documentation & folder name
    [Assembly 1.x_t, Assembly.x_t]
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2020-10-16 Integrates normal (non-pid) control system into development.
    In this commit, we integrate a normal guidance system that
    doesn't utilise a PID. Here we are using the same logic
    that we have tested within one of our testing projects
    `test_servo_mpu`. Here, we abstract some of the complexity
    into classes following the structure of the rest of the
    project.
    Within this commit, we also aim fix some of the build
    issues that had been experienced by some of the members
    within the team. Part of this also included tidying up the
    software and ensuring that it is in a tidy state to be
    delivered. Apologies that this is such a big commit. To
    implement these changes, I had created a new PIO project as
    I wa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
    [main.cpp, test_control.cpp]
2020-10-16 Fixes conflicts regarding sd_card testing.
    [test_sd.cpp]
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

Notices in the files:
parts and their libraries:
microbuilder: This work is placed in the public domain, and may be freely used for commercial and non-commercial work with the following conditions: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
